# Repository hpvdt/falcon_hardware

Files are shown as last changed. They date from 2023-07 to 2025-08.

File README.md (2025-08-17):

>[!WARNING]
>This repository is no longer being maintained. All board designs for Falcon are part of their respective project repositories under HPVDT. This repository can be considered a snapshot fo the project 2023 or so.

# Falcon Hardware

These are the collected files for all the custom circuit boards for the Falcon aircraft project. All circuits were designed in KiCad 7, and the Gerber files for the circuits as ordered are included.

These systems were primarily designed by several members of HPVDT, overseen by the head of electronics. A block diagram describing their place in the overaching system has been prepared.

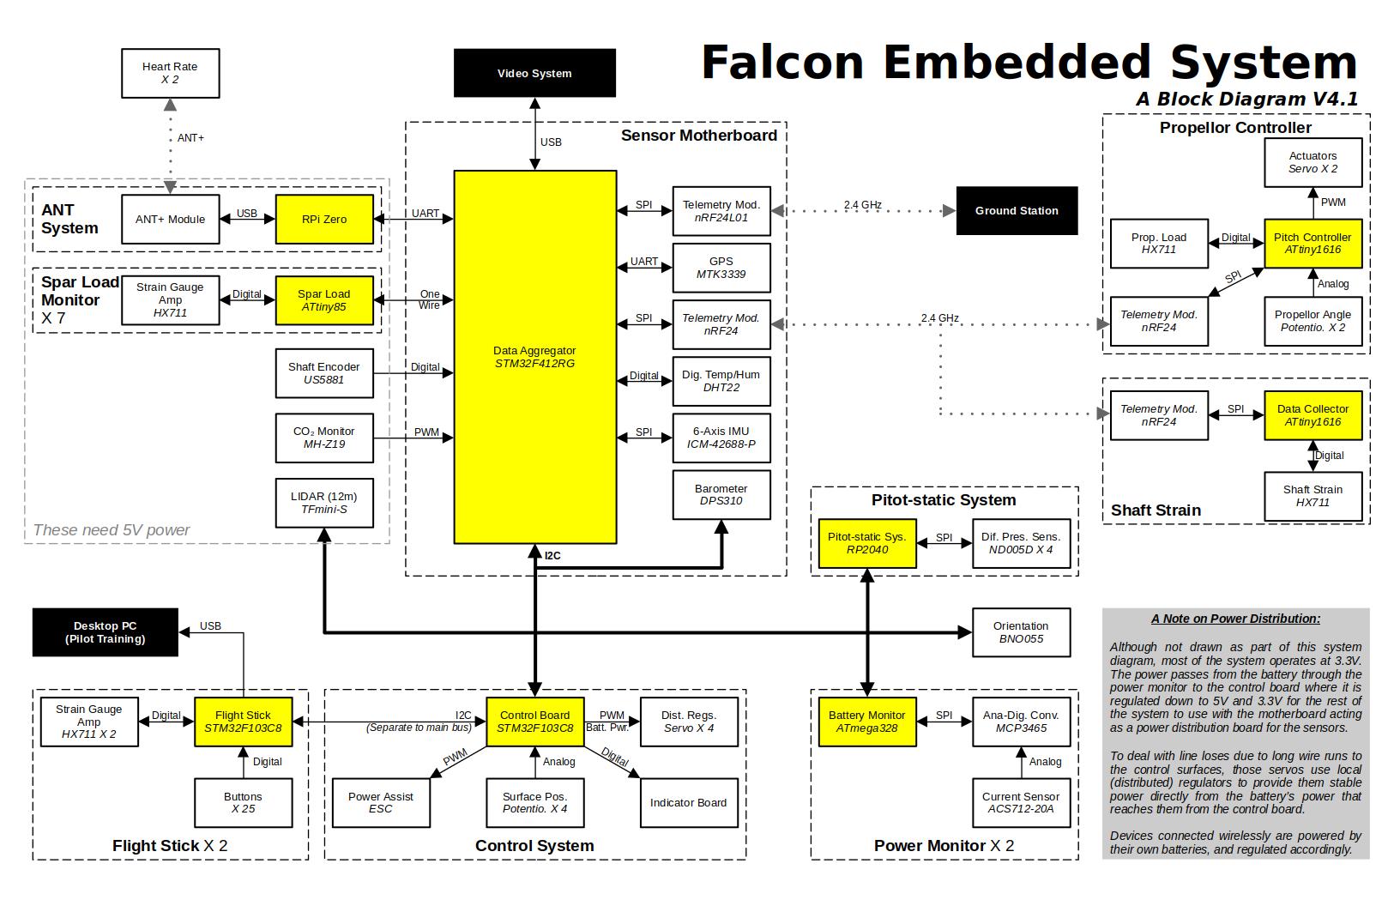
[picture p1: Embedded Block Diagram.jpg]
Embedded system block diagram


## Projects

Each folder is for a different electronics circuit/system, which are explained in the table below. 

| Folder | Project | Principal Designer |
| --- | ---| --- |
| `control` | Operates the aircraft's control surfaces | Abdullah Alsafar |
| `flight_stick` | Flight stick, pilots' primary input to the system | Aryan Ghosh |
| `indicator` | Daughter board to indicate control surface status to pilots | Abdullah Alsafar |
| `main_data` | Primary board for data collection of all sensor data | Aryan Ghosh |
| `pressure_sensor_array_atmega` | Differntial pressure array for monitoring wind (ATmega328P) | Jaden Stanshall |
| `pressure_sensor_array_rp` | Differntial pressure array for monitoring wind (RP2040) | Jaden Stanshall |
| `pressure_sensor_array_breakout` | Breakpout for our selected differential pressure sensors | Jaden Stanshall |
| `prop_pitch` | Adjusts the propellor blade pitch and monitors shaft loading | Savo Bajic |
| `servo_regulator` | Distributed servo voltage regulators | Abdullah Alsafar |
| `spar_sensor` | System to monitor the loading of our spars | Alya / Ishi |

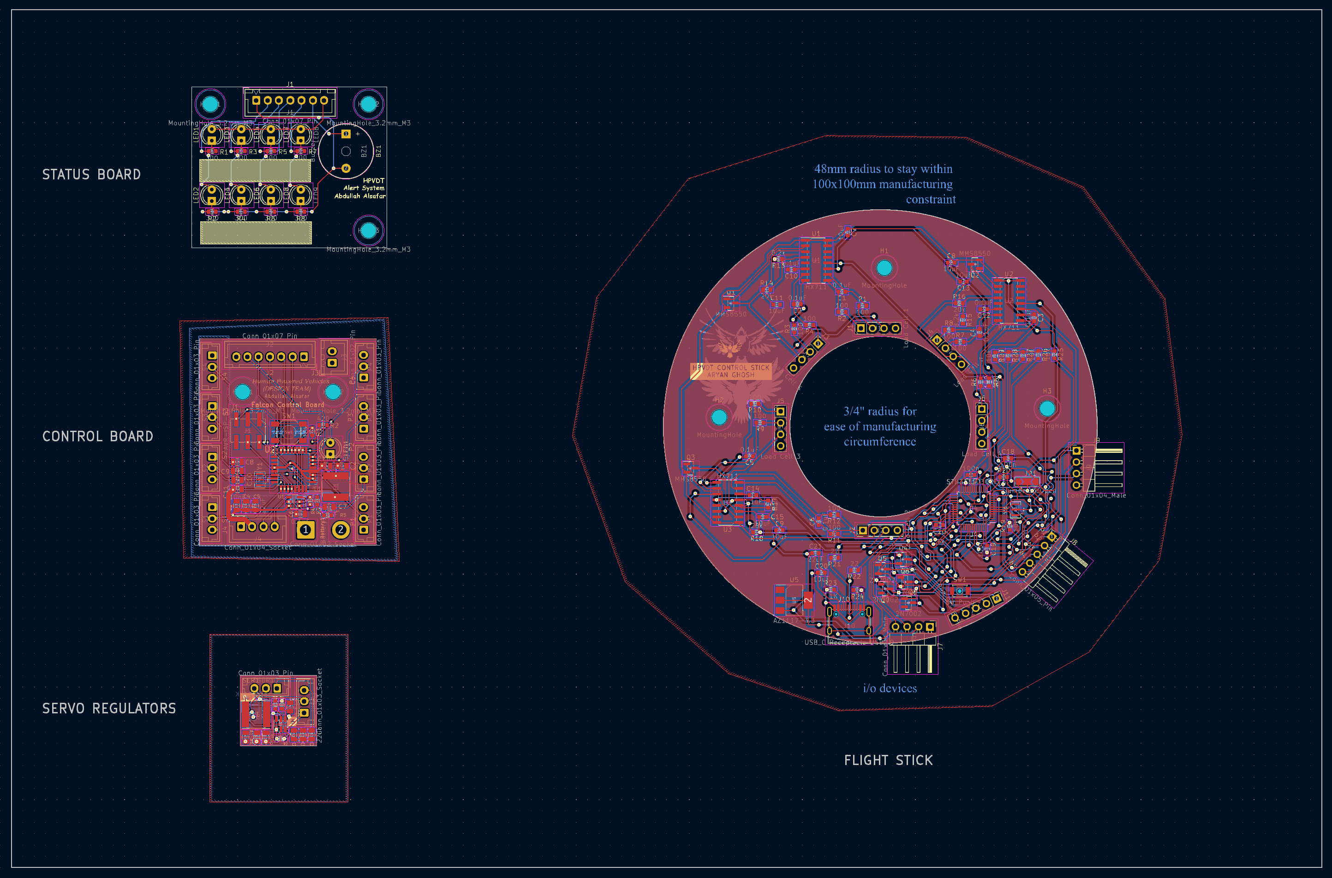
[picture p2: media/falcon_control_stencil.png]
Control system stencil / boards overview


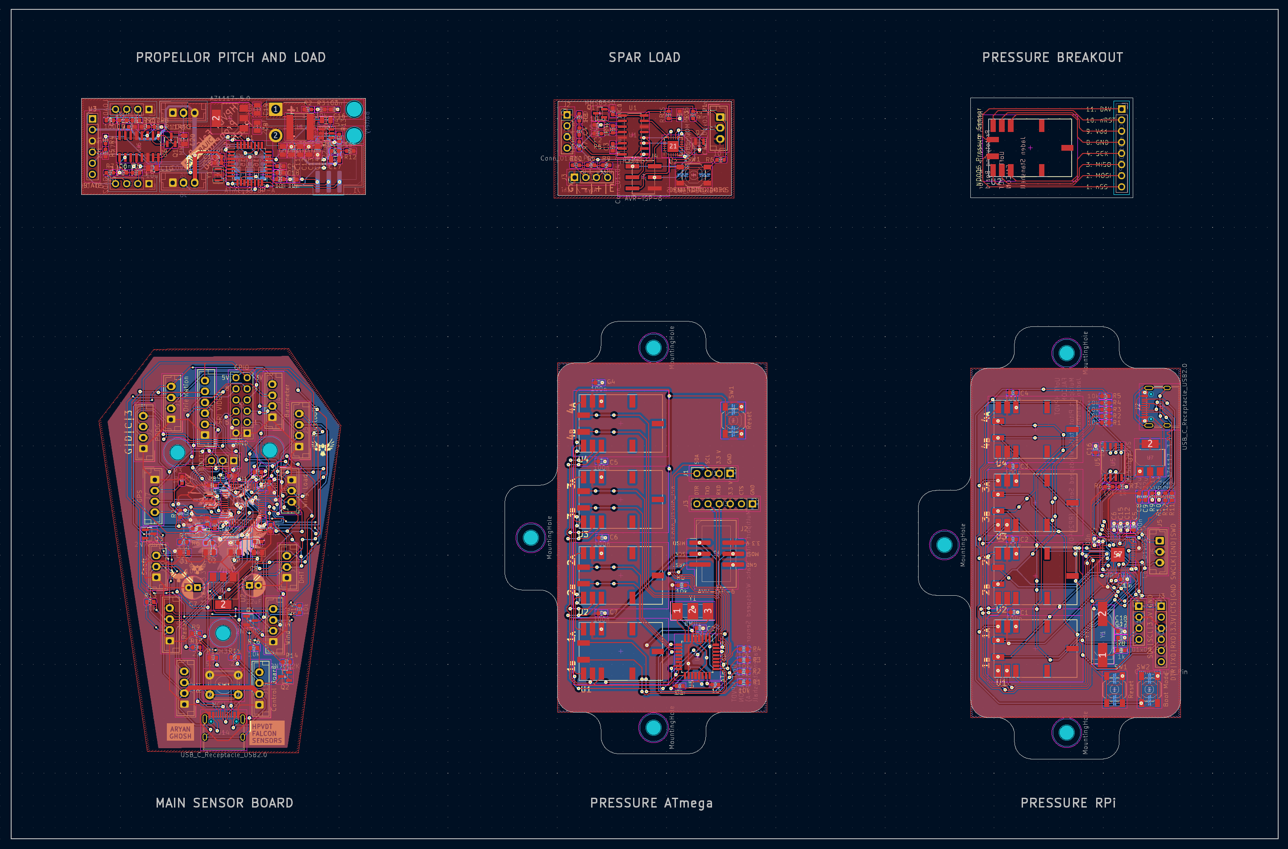
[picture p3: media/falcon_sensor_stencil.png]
Sensing system stencil / boards overview


## Additional Folders

In addition to these projects there are a couple extra folders not directly related to hardware projects present.

| Folder | Purpose | 
| --- | --- |
| `ordered_gerbers` | The manufacturing files actually used for the boards |
| `stencils` | The stencils prepared for the set of boards | 
| `media` | Media files for this repository |

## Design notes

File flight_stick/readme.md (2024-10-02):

# Falcon Aircraft Flight Stick
### In Progress

Human Powered Vehicles Design Team

November 2022

Aryan Ghosh

### Block diagram


#### Schematic Layout


### PCB 2-Layer Layout



### 3D Render of PCB Layout


## Introduction
Created for the Falcon Aircraft, the Falcon Aircraft Flight Stick (FAFS) is the first flight stick to implement **three** axes of motion detection, remain rigid, and feature up to 25 programmable buttons. This was done to accommodate the unique nature of the Human-powered falcon aircraft, where the user could control the entire aircraft with one hand, keeping the other free, while maintaining a durable and versatile design. 

The design features:
- An STM32 Microcontroller programmed with custom firmware and libraries
- An ADS131 amplifier and ADC paired with linear and torque strain gauges
- A 5x5 transistor array to feature up to 25 buttons
- Power indicators and Multi-colour LEDs to indicate device function
- USB-C connectivity to plug into a computer to use as a joystick
- STLinkV3 programmability with SWD and UART

ReadMe in progress...

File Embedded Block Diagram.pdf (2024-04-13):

## Shaft Strain

Pitot-static Sys.
RP2040

Dif. Pres. Sens.
ND005D X 4

LIDAR (12m)
TFmini-S

Flight Stick
STM32F103C8

Strain Gauge
Amp
HX711 X 2

Data Aggregator
STM32F412RG

Orientation
BNO055

Barometer
DPS310

GPS
MTK3339
ANT+ Module | RPi Zero

Strain Gauge
Amp
HX711

Spar Load
ATtiny85

Dist. Regs.
Servo X 4

Control Board
STM32F103C8

Surface Pos.
Potentio. X 4 | Indicator Board

Prop. Load
HX711

Buttons
X 25

Actuators
Servo X 2

Pitch Controller
ATtiny1616

Telemetry Mod.
nRF24

Telemetry Mod.
nRF24L01

Shaft Encoder
US5881

Video System Heart Rate
X 2

Battery Monitor
ATmega328

Ana-Dig. Conv.
MCP3465

Current Sensor
ACS712-20A

Dig. Temp/Hum
DHT22

Ground Station

## Spar Load Monitor

X 7

## ANT System

## Flight Stick X 2

## Pitot-static System

## Propellor Controller

Control System | Power Monitor X 2

SPI

SPI

One
Wire

UART

UART

Digital

USB

Digital

Digital

Digital

Digital

2.4 GHz

I2C

Digital | Analog | Analog

PWM

Shaft Strain
HX711

Data Collector
ATtiny1616

Telemetry Mod.
nRF24

SPI

Digital

SPI

Digital

PWM
Batt. Pwr.

## Sensor Motherboard

2.4 GHz

I2C
(Separate to main bus)

A Note on Power Distribution:

Although not drawn as part of this system diagram, most of the system operates at 3.3V. The power passes from the battery through the power monitor to the control board where it is regulated down to 5V and 3.3V for the rest of the system to use with the motherboard acting as a power distribution board for the sensors.

To deal with line loses due to long wire runs to the control surfaces, those servos use local (distributed) regulators to provide them stable power directly from the battery’s power that reaches them from the control board.

Devices connected wirelessly are powered by their own batteries, and regulated accordingly.

## These need 5V power

# Falcon Embedded System

## A Block Diagram V4.1

Telemetry Mod.
nRF24

SPI

6-Axis IMU
ICM-42688-P

SPI

SPI

Power Assist
ESC

PWM

CO2 Monitor
MH-Z19

PWM

ANT+

Desktop PC
(Pilot Training)

Propellor Angle
Potentio. X 2

Analog

USB

USB

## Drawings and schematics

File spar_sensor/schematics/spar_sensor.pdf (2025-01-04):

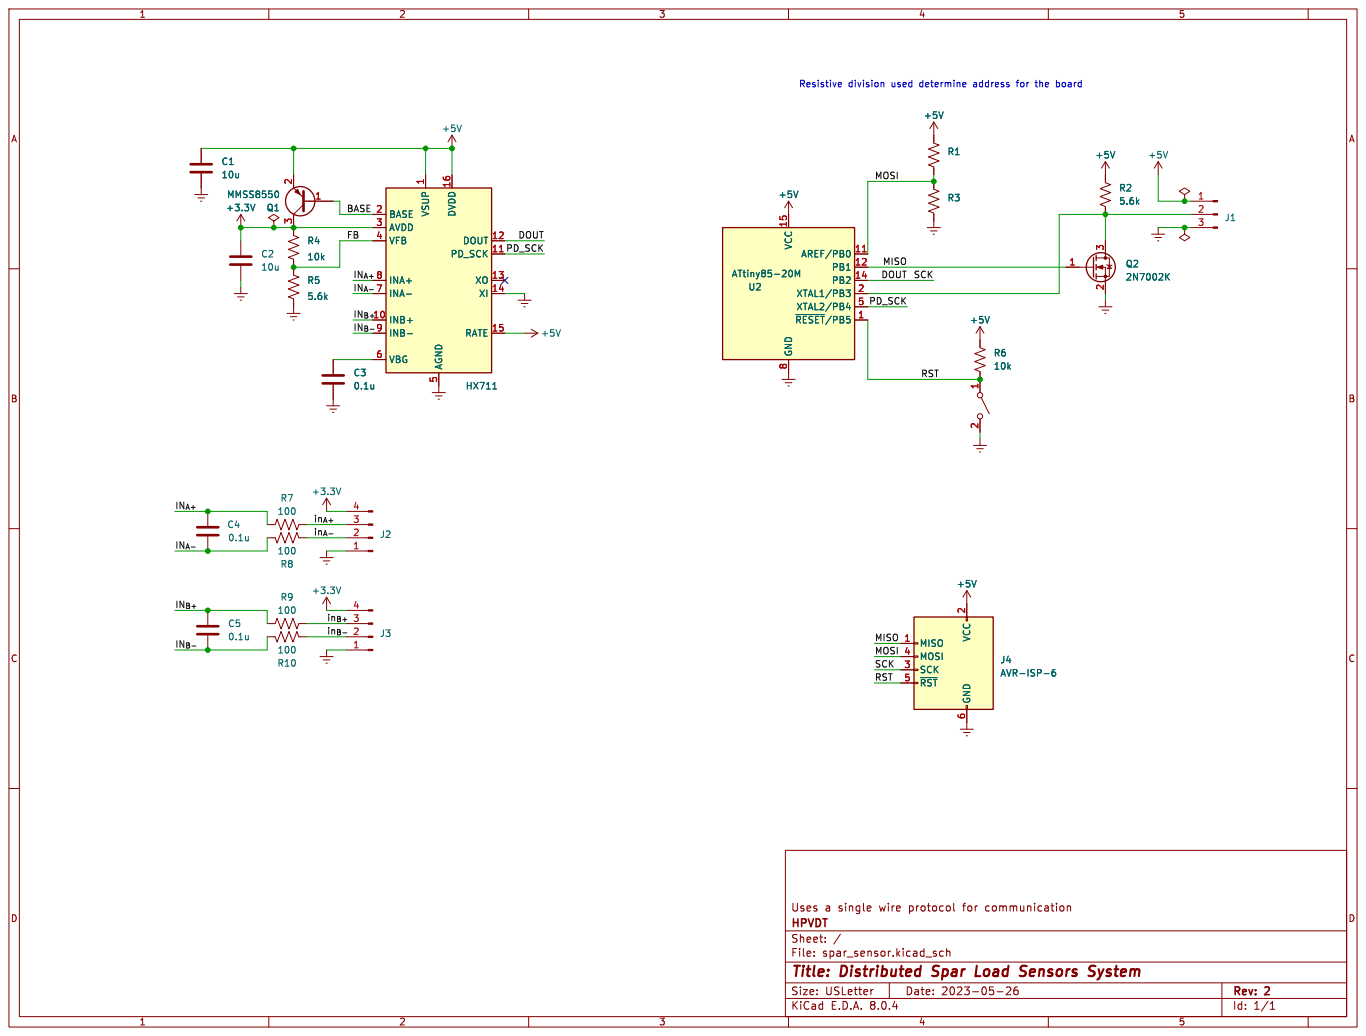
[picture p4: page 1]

2 SCK 3 MOSI 4 ~{RST} 5 GND

Id: 1/1 Title: Distributed Spar Load Sensors System

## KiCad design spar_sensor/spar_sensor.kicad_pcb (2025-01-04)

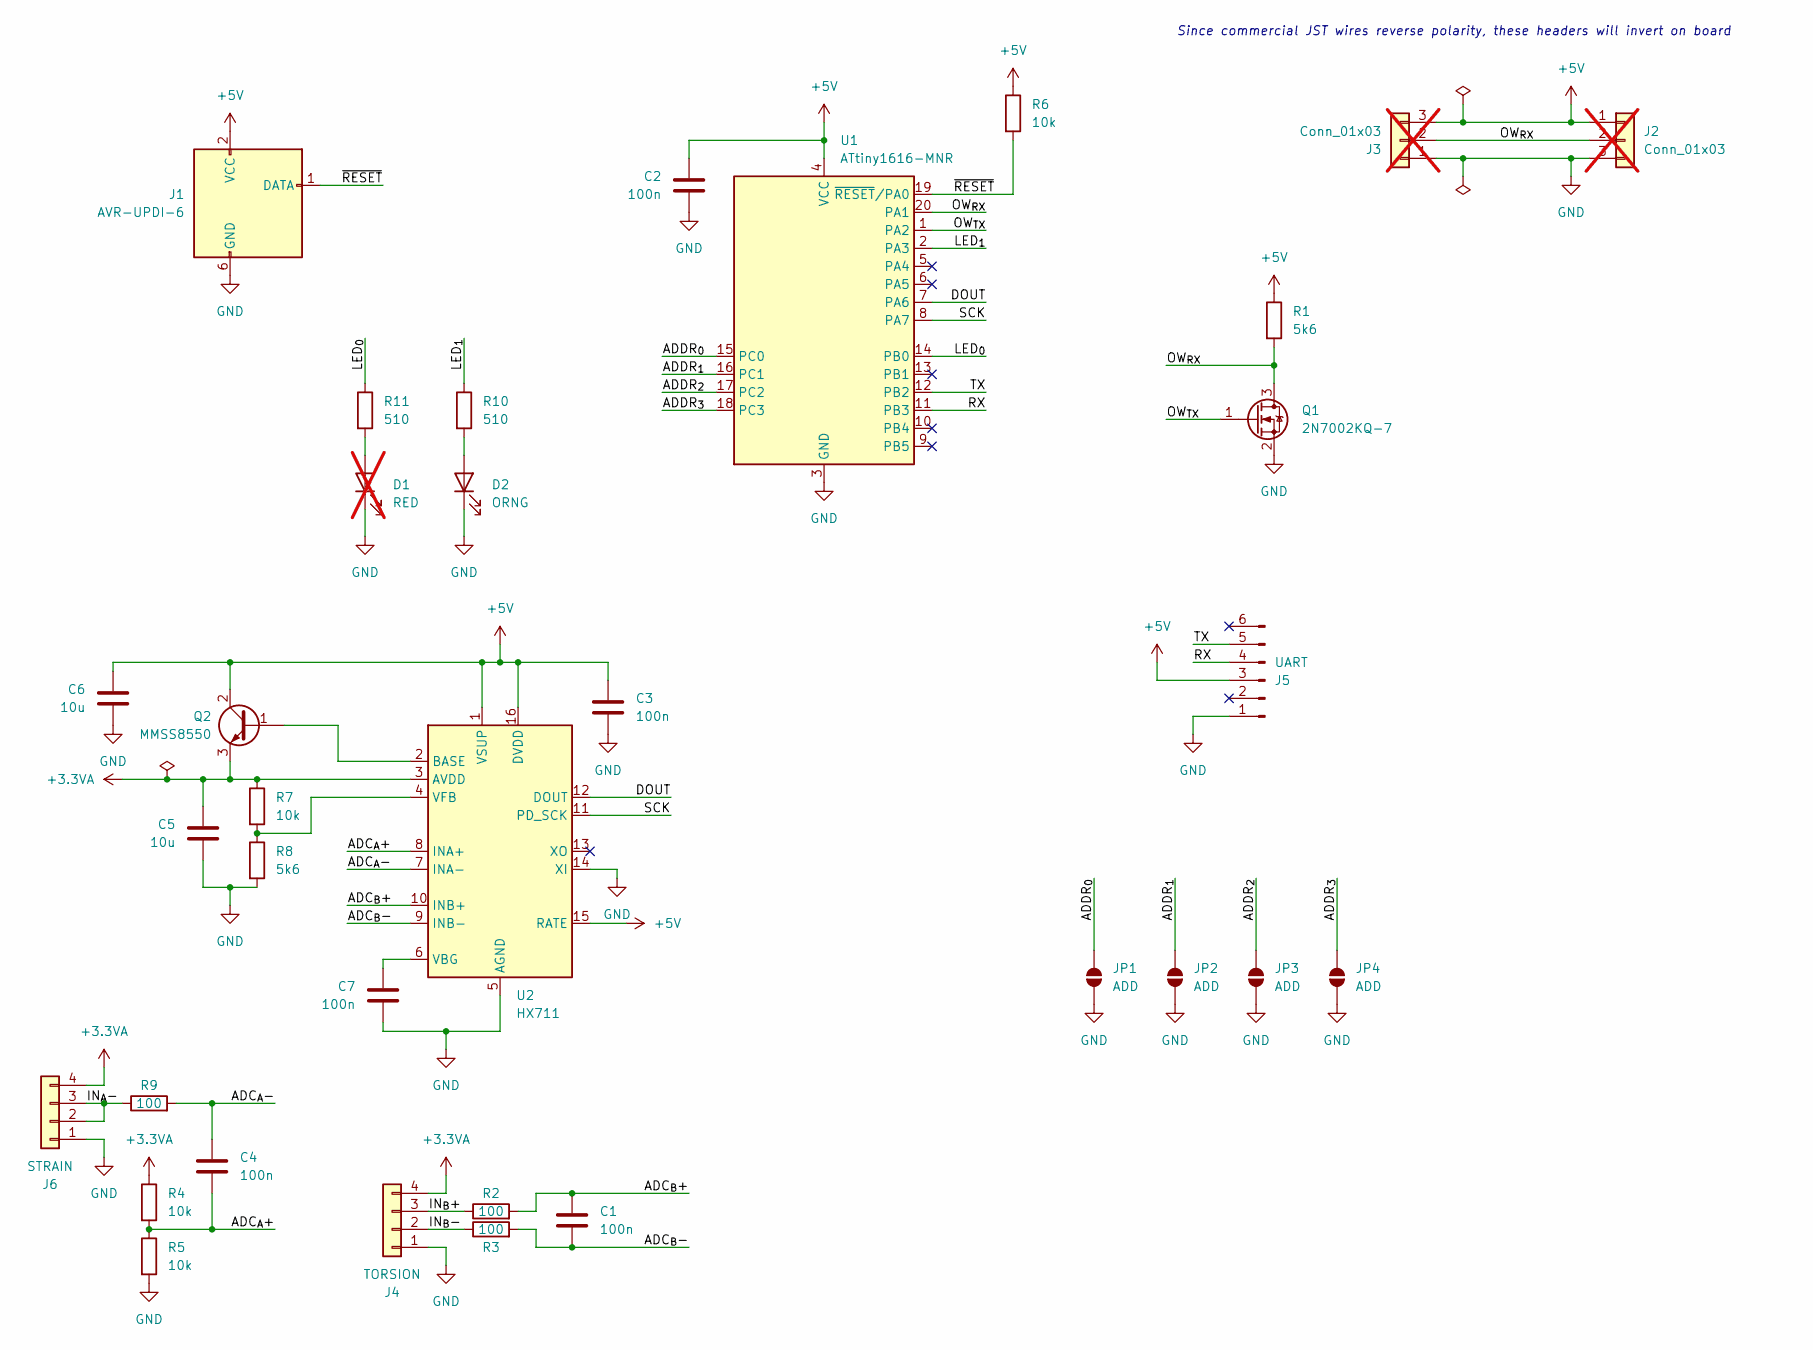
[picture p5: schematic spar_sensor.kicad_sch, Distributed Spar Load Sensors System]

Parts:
C1, C2, C3, C4, C7: 100n; C_0402_1005Metric; LCSC C5448875
C5, C6: 10u; C_0603_1608Metric; LCSC C5360828
D1: RED; LED_0805_2012Metric; LCSC N/A; not fitted
D2: ORNG; LED_0805_2012Metric; LCSC C2292
J1: AVR-UPDI-6; Tag-Connect_TC2030-IDC-NL_2x03_P1.27mm_Vertical; LCSC N/A
J2, J3: Conn_01x03; JST_EH_B3B-EH-A_1x03_P2.50mm_Vertical; LCSC C398546; not fitted
J4: TORSION; PinHeader_1x04_P2.00mm_Vertical; LCSC N/A
J5: UART; PinHeader_1x06_P2.54mm_Vertical; LCSC N/A
J6: STRAIN; PinHeader_1x04_P2.00mm_Vertical; LCSC N/A
JP1, JP2, JP3, JP4: ADD; SolderJumper-2_P1.3mm_Open_TrianglePad1.0x1.5mm; LCSC N/A
Q1: 2N7002KQ-7; SOT-23; LCSC C111971
Q2: MMSS8550; SOT-23; LCSC C192429
R1, R8: 5k6; R_0402_1005Metric; LCSC C340537
R2, R3, R9: 100; R_0402_1005Metric; LCSC C606168
R4, R5: 10k; R_0402_1005Metric; LCSC C191915
R6, R7: 10k; R_0402_1005Metric; LCSC C723353
R10, R11: 510; R_0402_1005Metric; LCSC C2991609
U1: ATtiny1616-MNR; VQFN-20-1EP_3x3mm_P0.4mm_EP1.7x1.7mm; LCSC C507118
U2: HX711; SOP-16_3.9x9.9mm_P1.27mm; LCSC C6705483

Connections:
+3.3VA: C5.1, J4.4, J6.4, Q2.3 (E), R4.1, R7.1, U2.3 (AVDD)
+5V: C2.1, C3.1, C6.1, J1.2 (VCC), J2.1, J3.3, J5.3, Q2.2 (C), R1.1, R6.1, U1.4 (VCC), U2.1 (VSUP), U2.15 (RATE), U2.16 (DVDD)
/ADC_{A}+: C4.2, R4.2, R5.1, U2.8 (INA+)
/ADC_{A}-: C4.1, R9.2, U2.7 (INA-)
/ADC_{B}+: C1.1, R2.2, U2.10 (INB+)
/ADC_{B}-: C1.2, R3.2, U2.9 (INB-)
/ADDR_{0}: JP1.2 (B), U1.15 (PC0)
/ADDR_{1}: JP2.2 (B), U1.16 (PC1)
/ADDR_{2}: JP3.2 (B), U1.17 (PC2)
/ADDR_{3}: JP4.2 (B), U1.18 (PC3)
/DOUT: U1.7 (PA6), U2.12 (DOUT)
/IN_{A}-: J6.2, J6.3, R9.1
/IN_{B}+: J4.3, R2.1
/IN_{B}-: J4.2, R3.1
/LED_{0}: R11.1, U1.14 (PB0)
/LED_{1}: R10.1, U1.2 (PA3)
/OW_{RX}: J2.2, J3.2, Q1.3 (D), R1.2, U1.20 (PA1)
/OW_{TX}: Q1.1 (G), U1.1 (PA2)
/RX: J5.4, U1.11 (PB3)
/SCK: U1.8 (PA7), U2.11 (PD_SCK)
/TX: J5.5, U1.12 (PB2)
/~RESET: J1.1 (DATA), R6.2, U1.19 (~RESET/PA0)
GND: C2.2, C3.2, C5.2, C6.2, C7.2, D1.1 (K), D2.1 (K), J1.6 (GND), J2.3, J3.1, J4.1, J5.1, J6.1, JP1.1 (A), JP2.1 (A), JP3.1 (A), JP4.1 (A), Q1.2 (S), R5.2, R8.2, U1.3 (GND), U1.21 (GND), U2.5 (AGND), U2.14 (XI)
unnamed: D1.2 (A), R11.2
unnamed: D2.2 (A), R10.2
unnamed: Q2.1 (B), U2.2 (BASE)
unnamed: C7.1, U2.6 (VBG)
unnamed: R7.2, R8.1, U2.4 (VFB)

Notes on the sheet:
Since commercial JST wires reverse polarity, these headers will invert on board

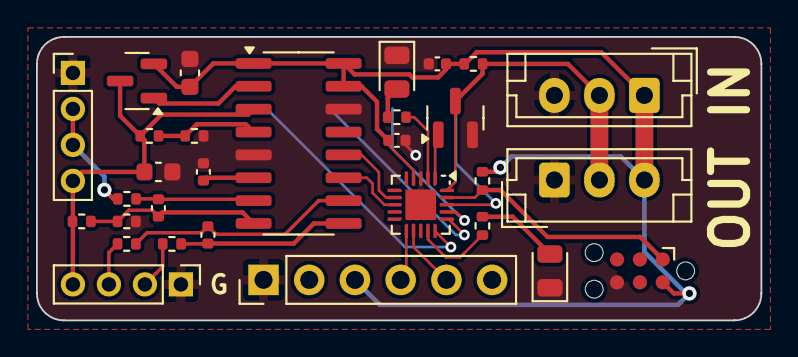
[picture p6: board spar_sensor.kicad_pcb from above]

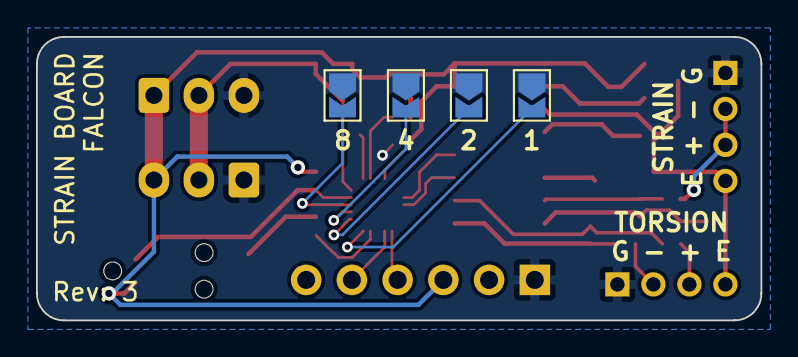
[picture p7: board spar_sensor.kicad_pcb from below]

Board: 2 copper layers, 40.2 x 15.8 mm, 34 parts (4 on the bottom side), 28 nets.

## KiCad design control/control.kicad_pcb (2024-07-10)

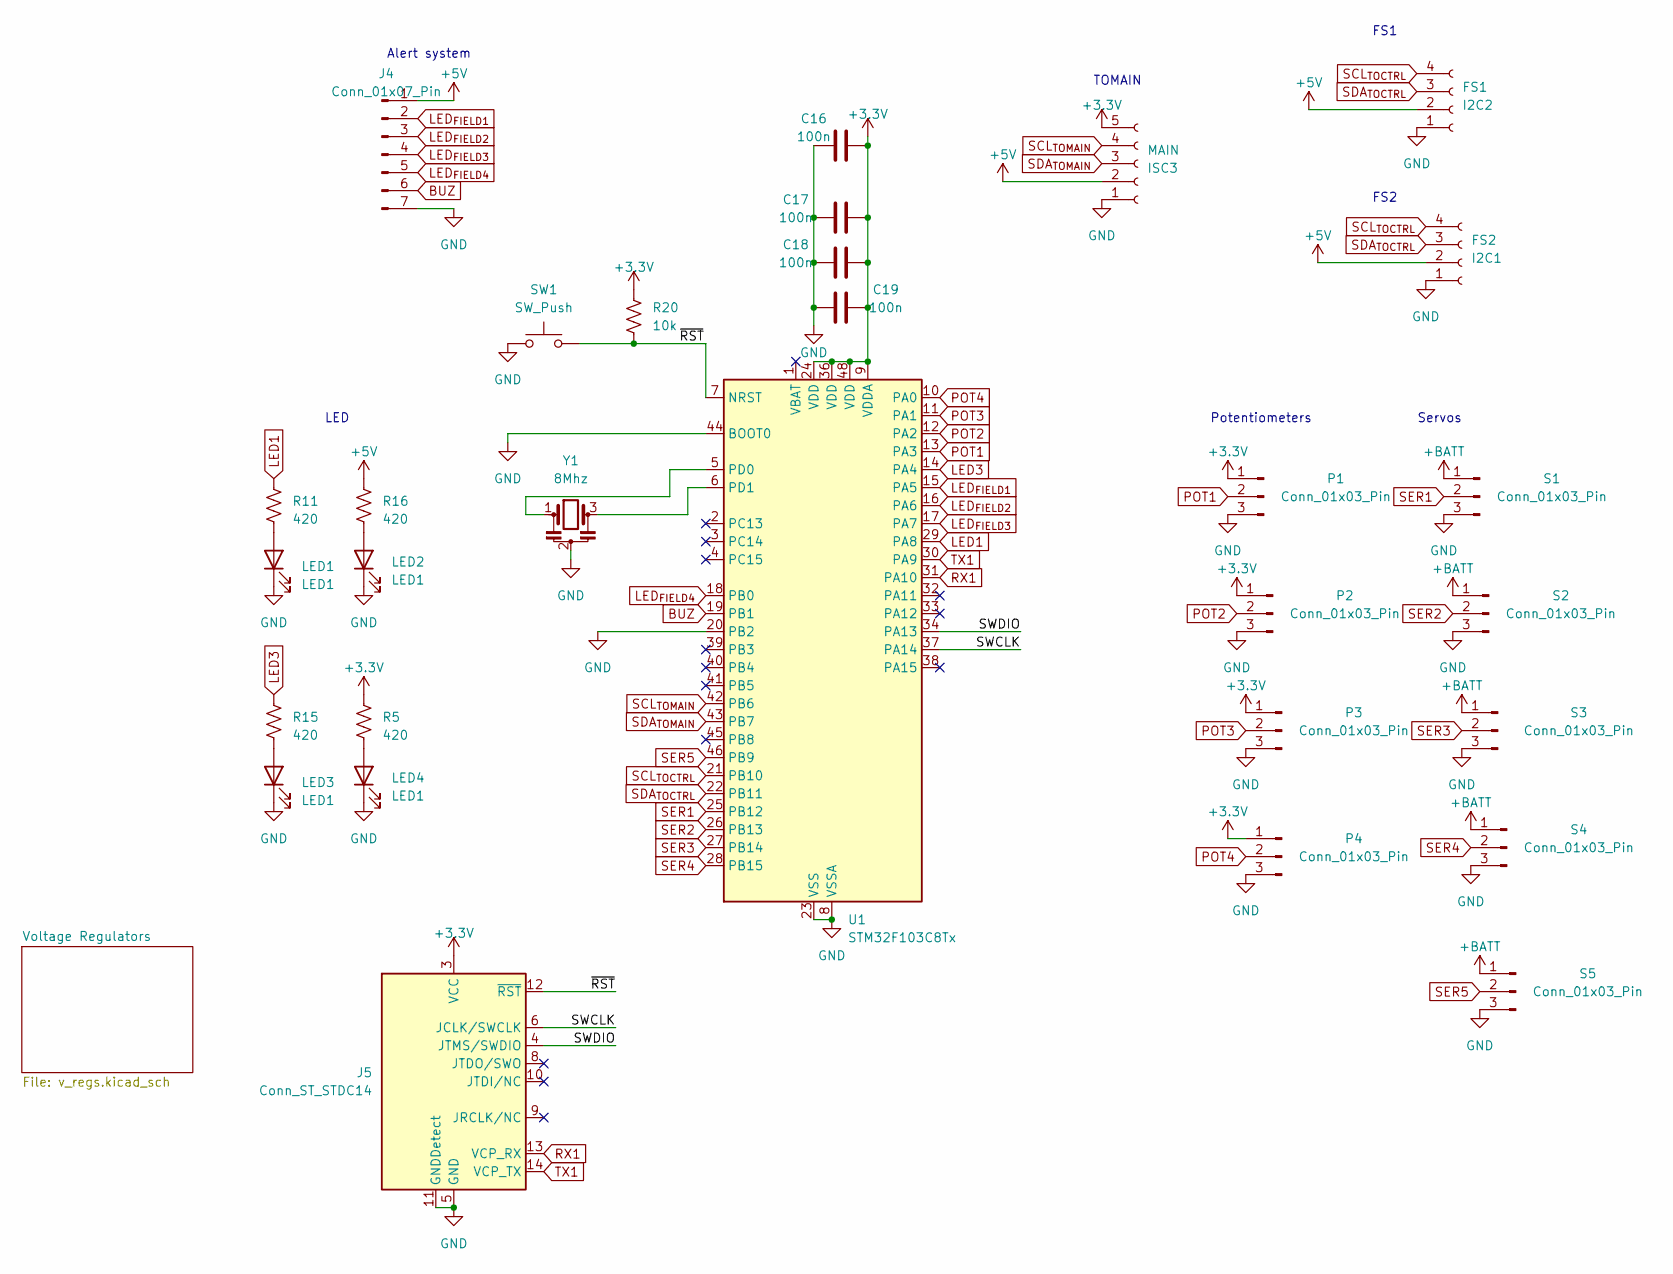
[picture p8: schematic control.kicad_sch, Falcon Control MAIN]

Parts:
C16, C17, C18, C19: 100n; C_0603_1608Metric
I2C1: FS2; JST_XH_B4B-XH-A_1x04_P2.50mm_Vertical
I2C2: FS1; JST_XH_B4B-XH-A_1x04_P2.50mm_Vertical
ISC3: MAIN; JST_XH_B5B-XH-A_1x05_P2.50mm_Vertical
J4: Conn_01x07_Pin; JST_XH_B7B-XH-A_1x07_P2.50mm_Vertical
J5: Conn_ST_STDC14; PinHeader_2x07_P1.27mm_Vertical_SMD
LED1, LED2, LED3, LED4: LED1; LED_0805_2012Metric_Pad1.15x1.40mm_HandSolder
P1, P2, P3, P4: Conn_01x03_Pin; JST_EH_B3B-EH-A_1x03_P2.50mm_Vertical
R5, R11, R15, R16: 420; R_0603_1608Metric
R20: 10k; R_0603_1608Metric
S1, S2, S3, S4, S5: Conn_01x03_Pin; JST_EH_B3B-EH-A_1x03_P2.50mm_Vertical
SW1: SW_Push; SW_SPST_B3U-1000P-B
U1: STM32F103C8Tx; LQFP-48_7x7mm_P0.5mm
Y1: 8Mhz; Resonator_SMD_Murata_CSTxExxV-3Pin_3.0x1.1mm

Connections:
+5V: I2C1.2, I2C2.2, ISC3.2, J4.1, R16.2; also elsewhere on the board
/SWCLK: J5.6 (JCLK/SWCLK), U1.37 (PA14)
/SWDIO: J5.4 (JTMS/SWDIO), U1.34 (PA13)
/~RST: J5.12 (~RST), U1.7 (NRST); also elsewhere on the board
BUZ: J4.6, U1.19 (PB1)
LED1: R11.2, U1.29 (PA8)
LED3: R15.2, U1.14 (PA4)
LED_{FIELD1}: J4.2, U1.15 (PA5)
LED_{FIELD2}: J4.3, U1.16 (PA6)
LED_{FIELD3}: J4.4, U1.17 (PA7)
LED_{FIELD4}: J4.5, U1.18 (PB0)
unnamed: LED1.2 (A), R11.1
unnamed: LED2.2 (A), R16.1
unnamed: LED3.2 (A), R15.1
unnamed: LED4.2 (A), R5.1
unnamed: U1.5 (PD0), Y1.1
unnamed: U1.6 (PD1), Y1.3
POT1: P1.2, U1.13 (PA3)
POT2: P2.2, U1.12 (PA2)
POT3: P3.2, U1.11 (PA1)
POT4: P4.2, U1.10 (PA0)
RX1: J5.13 (VCP_RX), U1.31 (PA10)
SCL_{TOCTRL}: I2C1.4, I2C2.4, U1.21 (PB10)
SCL_{TOMAIN}: ISC3.4, U1.42 (PB6)
SDA_{TOCTRL}: I2C1.3, I2C2.3, U1.22 (PB11)
SDA_{TOMAIN}: ISC3.3, U1.43 (PB7)
SER1: S1.2, U1.25 (PB12)
SER2: S2.2, U1.26 (PB13)
SER3: S3.2, U1.27 (PB14)
SER4: S4.2, U1.28 (PB15)
SER5: S5.2, U1.46 (PB9)
TX1: J5.14 (VCP_TX), U1.30 (PA9)

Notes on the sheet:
FS1
Servos
Alert system
FS2
TOMAIN
Potentiometers
LED

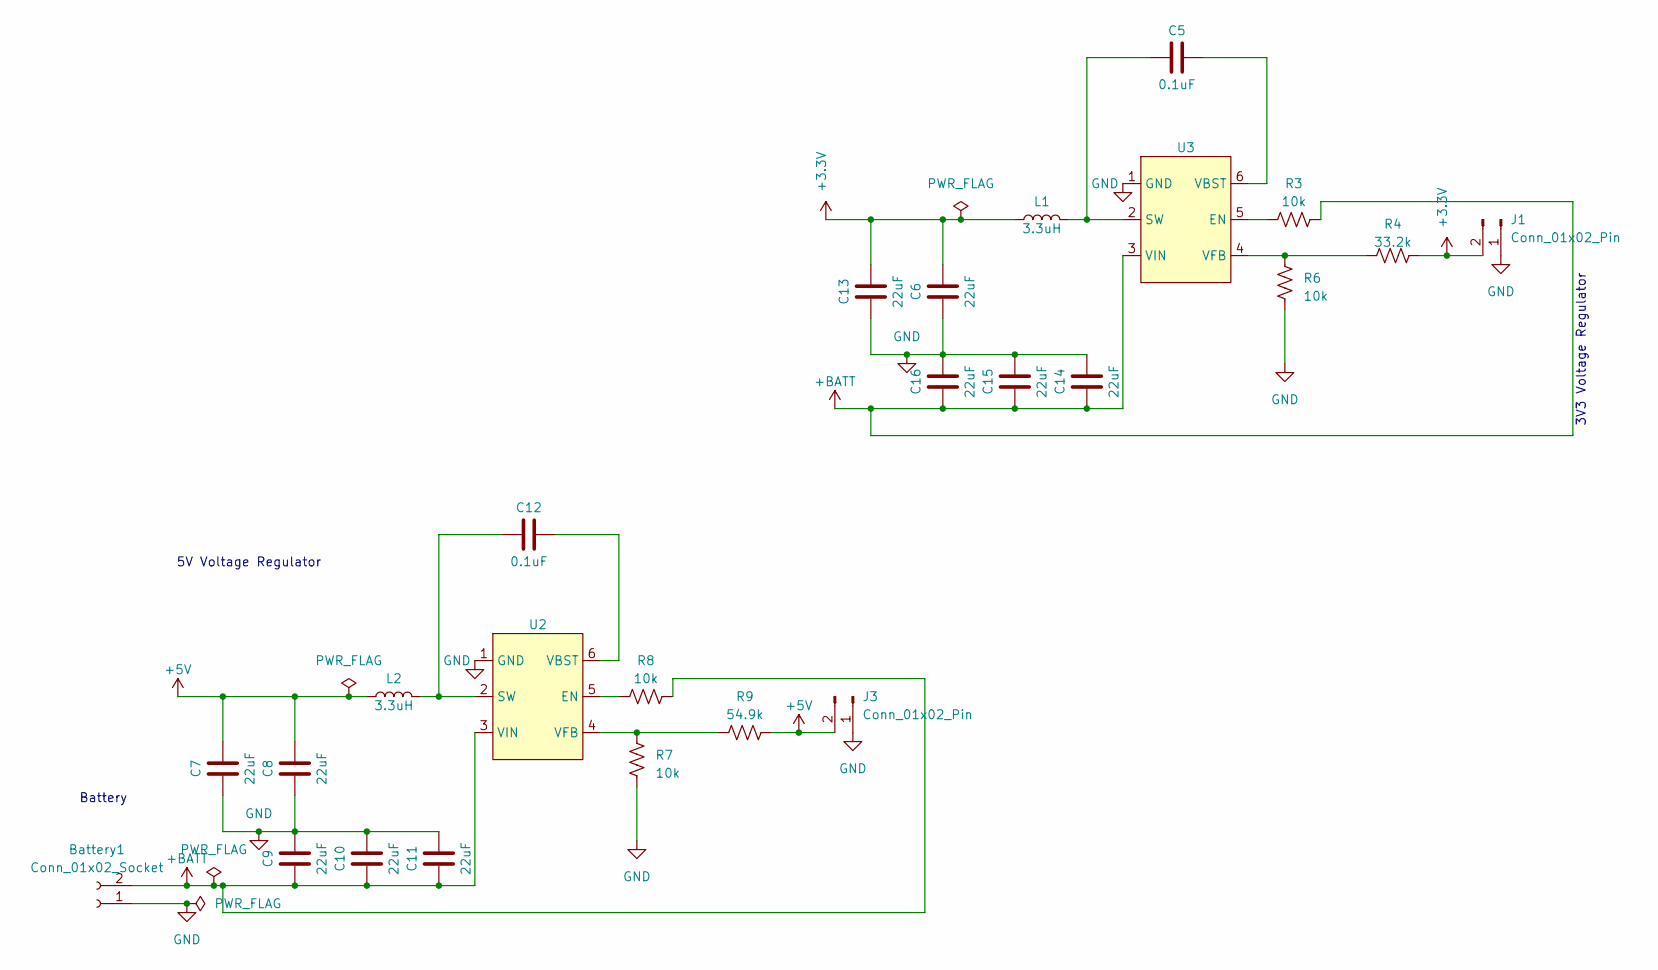
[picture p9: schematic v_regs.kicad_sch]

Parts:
Battery1: Conn_01x02_Socket; AMASS_XT60-M_1x02_P7.20mm_Vertical
C5, C12: 0.1uF; C_0805_2012Metric
C6, C7, C8, C9, C10, C11, C13, C14, C15, C16: 22uF; C_0805_2012Metric
J1, J3: Conn_01x02_Pin; JST_XH_B2B-XH-A_1x02_P2.50mm_Vertical
L1, L2: 3.3uH; L_Taiyo-Yuden_NR-60xx
R3, R6, R7, R8: 10k; R_0603_1608Metric
R4: 33.2k; R_0603_1608Metric
R9: 54.9k; R_0603_1608Metric
U2, U3: TSOT-23-6

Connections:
+5V: C7.2, C8.2, J3.2, L2.1, R9.1; also elsewhere on the board
unnamed: R8.1, U2.5 (EN)
unnamed: C12.1, L2.2, U2.2 (SW)
unnamed: C12.2, U2.6 (VBST)
unnamed: R7.2, R9.2, U2.4 (VFB)
unnamed: R3.1, U3.5 (EN)
unnamed: C5.1, L1.2, U3.2 (SW)
unnamed: C5.2, U3.6 (VBST)
unnamed: R4.2, R6.2, U3.4 (VFB)

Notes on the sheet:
5V Voltage Regulator
3V3 Voltage Regulator
Battery

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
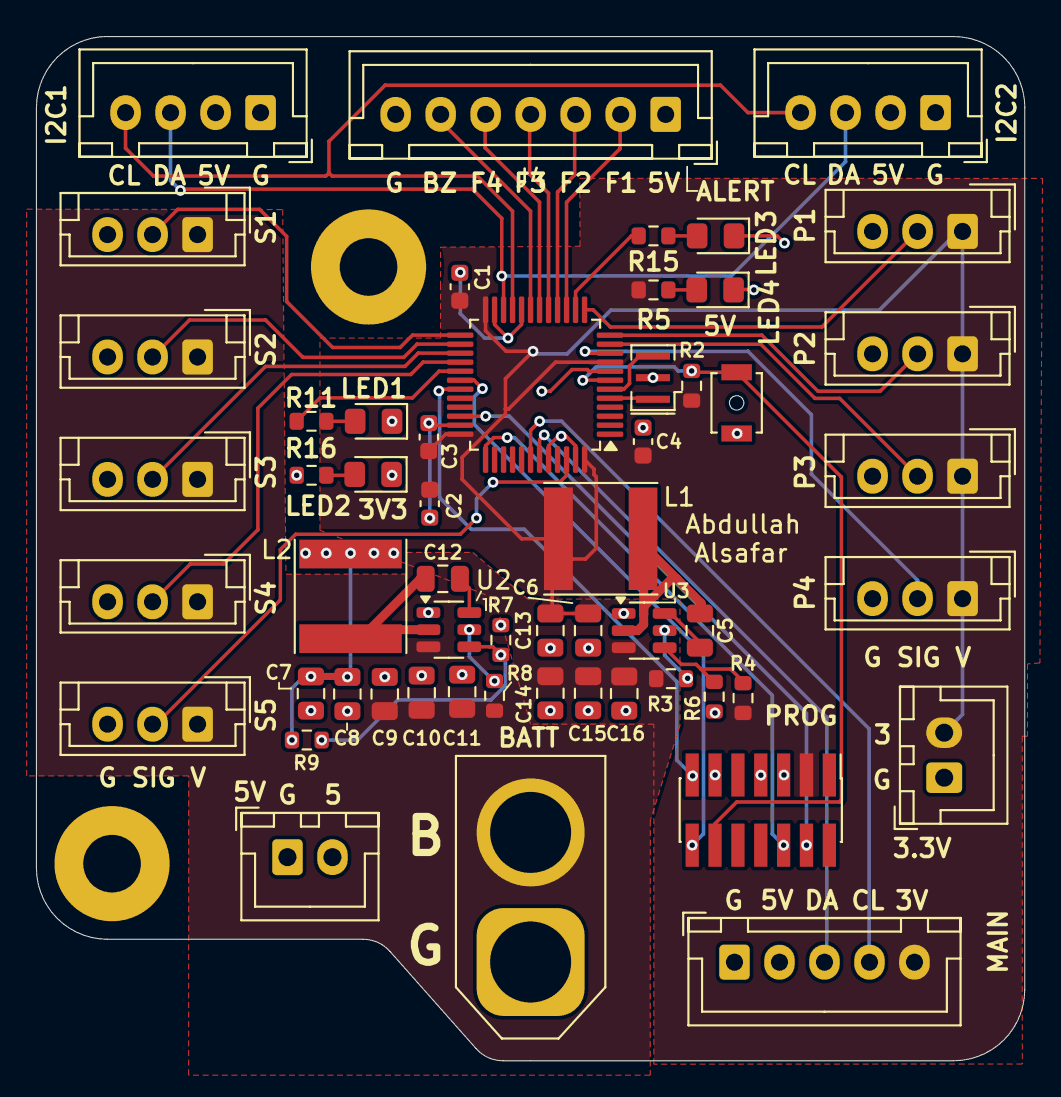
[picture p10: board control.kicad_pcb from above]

Board: 2 copper layers, 54.9 x 56.9 mm, 55 parts (0 on the bottom side), 43 nets.

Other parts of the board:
C1, C2, C3, C4: 100n; C_0603_1608Metric
R2: 10k; R_0603_1608Metric
SW2: SW_Push; SW_SPST_B3U-1000P-B

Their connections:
/~RST: R2.2, SW2.2; also elsewhere on the board

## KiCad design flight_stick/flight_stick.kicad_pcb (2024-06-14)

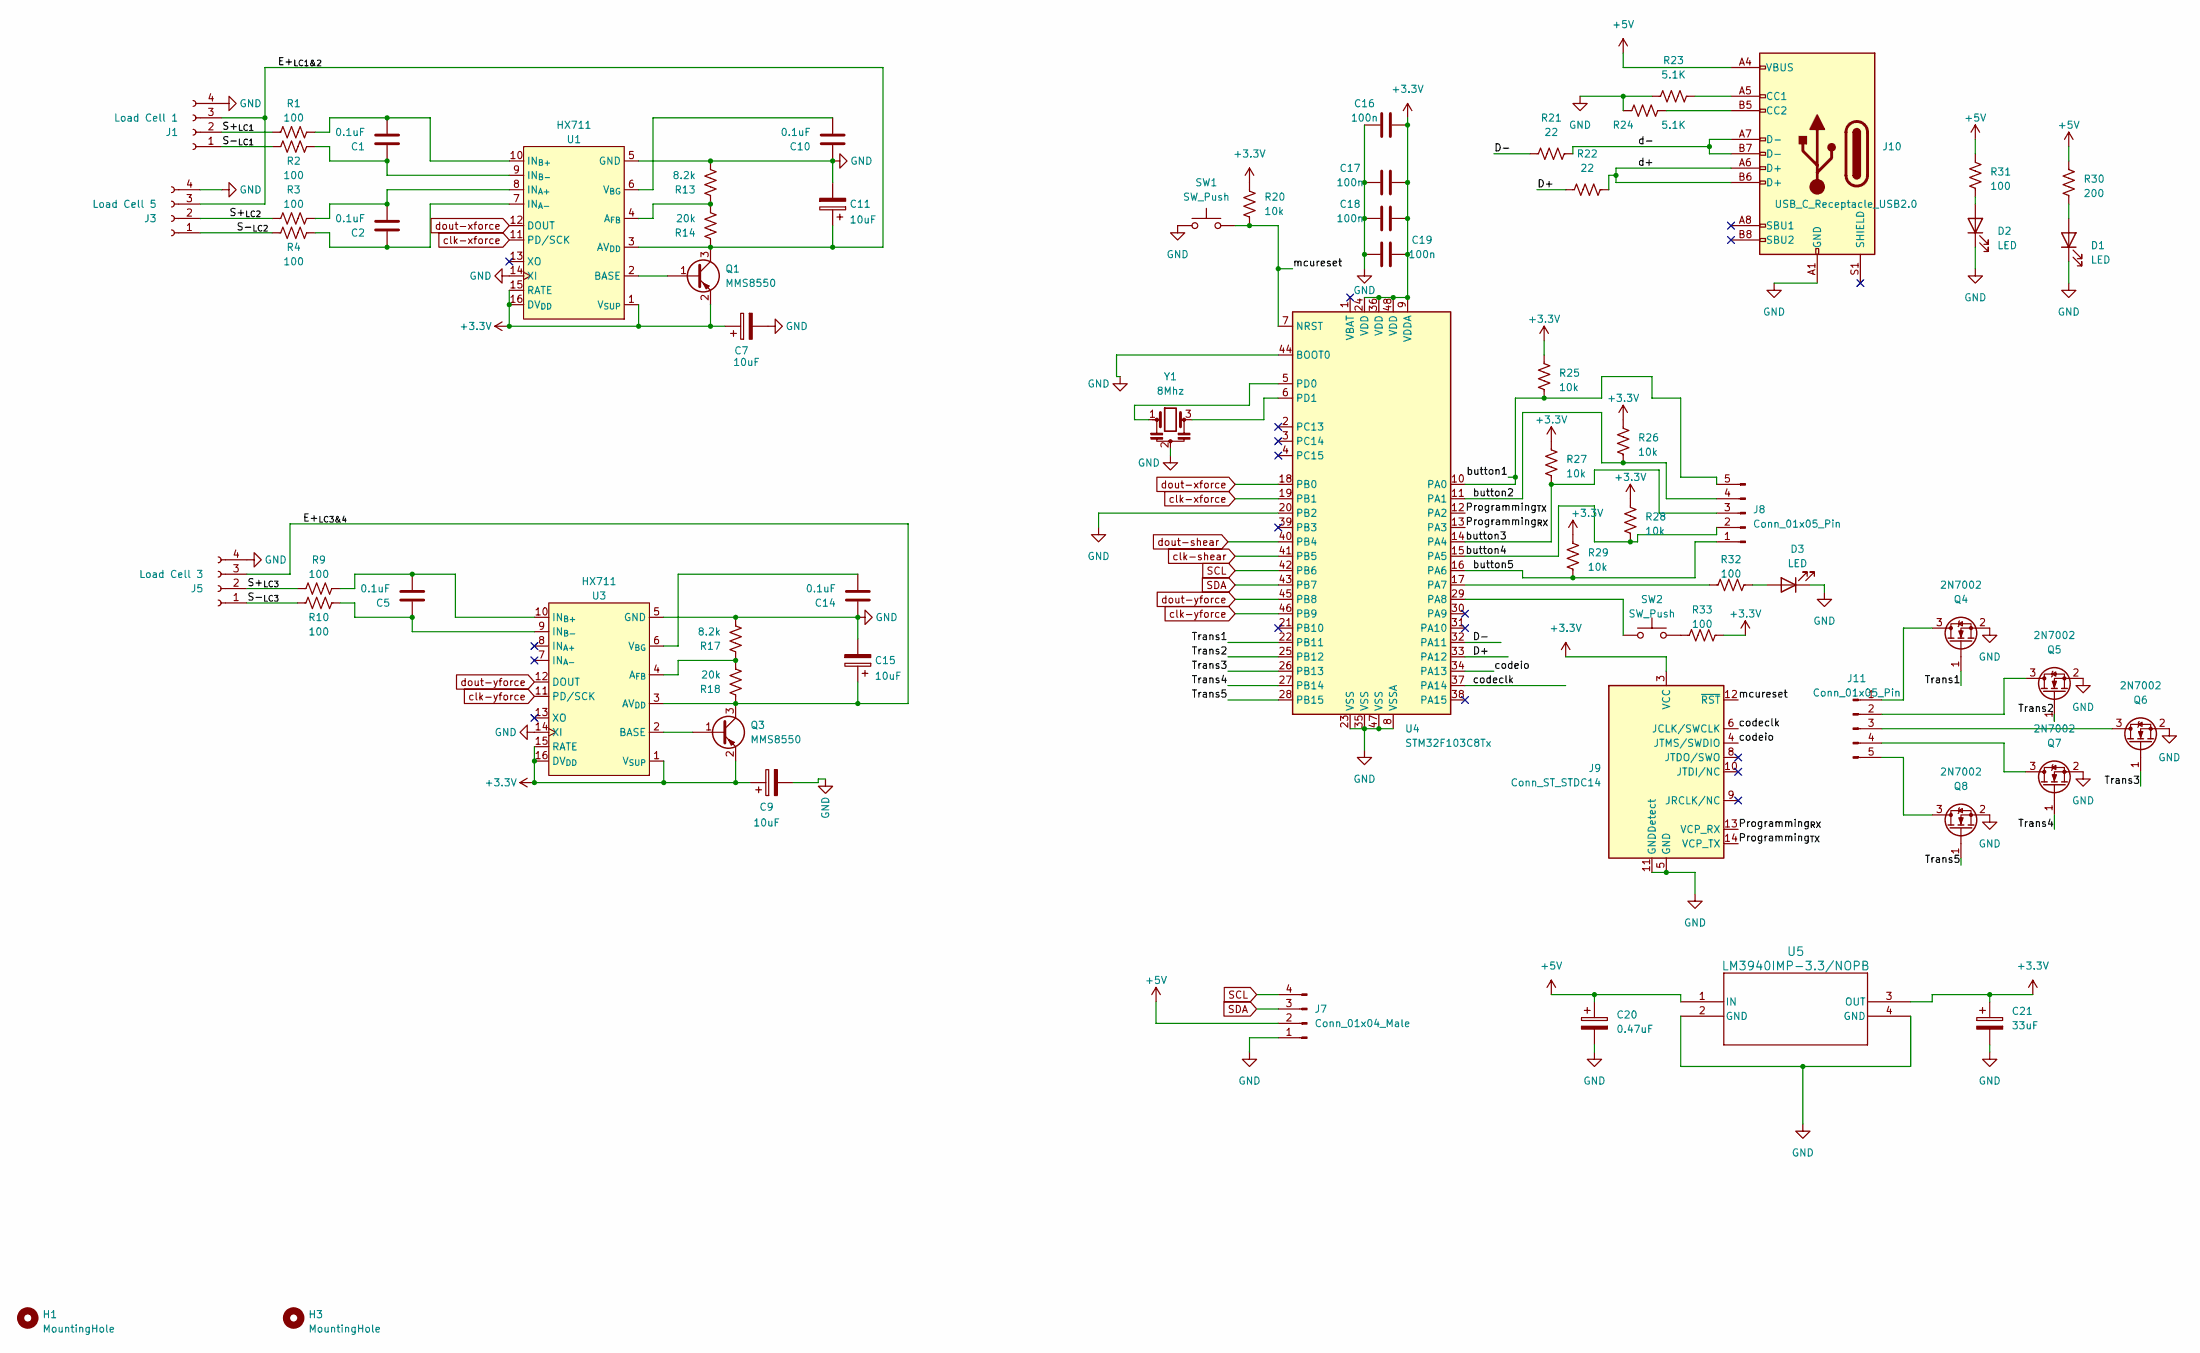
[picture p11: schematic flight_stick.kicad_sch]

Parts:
C1, C2, C5, C10, C14: 0.1uF; C_0603_1608Metric
C7, C9, C11, C15: 10uF; C_0603_1608Metric
C16, C17, C18, C19: 100n; C_0603_1608Metric
C20: 0.47uF; C_0603_1608Metric
C21: 33uF; C_0603_1608Metric
D1, D2, D3: LED; LED_2010_5025Metric
H1, H3: MountingHole; MountingHole_3.2mm_M3_ISO7380
J1: Load Cell 1; PinHeader_1x04_P1.00mm_Vertical
J3: Load Cell 5; PinHeader_1x04_P1.00mm_Vertical
J5: Load Cell 3; PinHeader_1x04_P1.00mm_Vertical
J7: Conn_01x04_Male; JST_XH_B4B-XH-A_1x04_P2.50mm_Vertical
J8: Conn_01x05_Pin; PinHeader_1x05_P2.54mm_Horizontal
J9: Conn_ST_STDC14; PinHeader_2x07_P1.27mm_Vertical_SMD
J10: USB_C_Receptacle_USB2.0; USB_C_Receptacle_HRO_TYPE-C-31-M-12
J11: Conn_01x05_Pin; PinHeader_1x05_P2.54mm_Vertical
Q1, Q3: MMS8550; SOT-23
Q4, Q5, Q6, Q7, Q8: 2N7002; SOT-23
R1, R2, R3, R4, R9, R10, R31, R32, R33: 100; R_0603_1608Metric
R13, R17: 8.2k; R_0603_1608Metric
R14, R18: 20k; R_0603_1608Metric
R20, R25, R26, R27, R28, R29: 10k; R_0603_1608Metric
R21, R22: 22; R_0603_1608Metric
R23, R24: 5.1K; R_0603_1608Metric
R30: 200; R_0603_1608Metric
SW1, SW2: SW_Push; SW_SPST_B3U-1000P-B
U1, U3: HX711; SOIC-16_3.9x9.9mm_P1.27mm
U4: STM32F103C8Tx; LQFP-48_7x7mm_P0.5mm
U5: LM3940IMP-3.3/NOPB; SOT-223
Y1: 8Mhz; Resonator_SMD_Murata_CSTxExxV-3Pin_3.0x1.1mm

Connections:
+3.3V: C7.1, C9.1, C16.2, C17.2, C18.2, C19.1, C21.1, J9.3 (VCC), Q1.2 (E), Q3.2 (E), R20.1, R25.1, R26.1, R27.1, R28.1, R29.1, R33.2, U1.1 (V_{SUP}), U1.15 (RATE), U1.16 (DV_{DD}), U3.1 (V_{SUP}), U3.15 (RATE), U3.16 (DV_{DD}), U4.9 (VDDA), U4.24 (VDD), U4.36 (VDD), U4.48 (VDD), U5.3 (OUT)
+5V: C20.1, J7.2, J10.A4 (VBUS), J10.A9 (VBUS), J10.B4 (VBUS), J10.B9 (VBUS), R30.1, R31.1, U5.1 (IN)
/D+: R22.1, U4.33 (PA12)
/D-: R21.1, U4.32 (PA11)
/E+_{LC1&2}: C11.1, J1.3, J3.3, Q1.3 (C), R14.1, U1.3 (AV_{DD})
/E+_{LC3&4}: C15.1, J5.3, Q3.3 (C), R18.1, U3.3 (AV_{DD})
/Programming_{RX}: J9.13 (VCP_RX), U4.13 (PA3)
/Programming_{TX}: J9.14 (VCP_TX), U4.12 (PA2)
/S+_{LC1}: J1.2, R1.1
/S+_{LC2}: J3.2, R3.1
/S+_{LC3}: J5.2, R9.1
/S-_{LC1}: J1.1, R2.1
/S-_{LC2}: J3.1, R4.1
/S-_{LC3}: J5.1, R10.1
/Trans1: Q4.1 (G), U4.22 (PB11)
/Trans2: Q5.1 (G), U4.25 (PB12)
/Trans3: Q6.1 (G), U4.26 (PB13)
/Trans4: Q7.1 (G), U4.27 (PB14)
/Trans5: Q8.1 (G), U4.28 (PB15)
/button1: J8.5, R25.2, U4.10 (PA0)
/button2: J8.4, R26.2, U4.11 (PA1)
/button3: J8.3, R27.2, U4.14 (PA4)
/button4: J8.2, R28.2, U4.15 (PA5)
/button5: J8.1, R29.2, U4.16 (PA6)
/codeclk: J9.6 (JCLK/SWCLK), U4.37 (PA14)
/codeio: J9.4 (JTMS/SWDIO), U4.34 (PA13)
/d+: J10.A6 (D+), J10.B6 (D+), R22.2
/d-: J10.A7 (D-), J10.B7 (D-), R21.2
/mcureset: J9.12 (~RST), R20.2, SW1.2, U4.7 (NRST)
GND: C7.2, C9.2, C10.2, C11.2, C14.2, C15.2, C16.1, C17.1, C18.1, C19.2, C20.2, C21.2, D1.1 (K), D2.1 (K), D3.1 (K), J1.4, J3.4, J5.4, J7.1, J9.5 (GND), J9.7 (GND), J9.11 (GNDDetect), J10.A1 (GND), J10.A12 (GND), J10.B1 (GND), J10.B12 (GND), Q4.2 (S), Q5.2 (S), Q6.2 (S), Q7.2 (S), Q8.2 (S), R13.2, R17.2, R23.1, R24.1, SW1.1, U1.5 (GND), U1.14 (XI), U3.5 (GND), U3.14 (XI), U4.8 (VSSA), U4.20 (PB2), U4.23 (VSS), U4.35 (VSS), U4.44 (BOOT0), U4.47 (VSS), U5.2 (GND), U5.4 (GND), Y1.2
unnamed: D1.2 (A), R30.2
unnamed: D2.2 (A), R31.2
unnamed: D3.2 (A), R32.2
unnamed: J10.A5 (CC1), R23.2
unnamed: J10.B5 (CC2), R24.2
unnamed: J11.1, Q4.3 (D)
unnamed: J11.2, Q5.3 (D)
unnamed: J11.3, Q6.3 (D)
unnamed: J11.4, Q7.3 (D)
unnamed: J11.5, Q8.3 (D)
unnamed: Q1.1 (B), U1.2 (BASE)
unnamed: Q3.1 (B), U3.2 (BASE)
unnamed: R33.1, SW2.2
unnamed: R13.1, R14.2, U1.4 (A_{FB})
unnamed: C2.1, R3.2, U1.8 (IN_{A+})
unnamed: C2.2, R4.2, U1.7 (IN_{A-})
unnamed: C1.1, R1.2, U1.10 (IN_{B+})
unnamed: C1.2, R2.2, U1.9 (IN_{B-})
unnamed: C10.1, U1.6 (V_{BG})
unnamed: R17.1, R18.2, U3.4 (A_{FB})
unnamed: C5.1, R9.2, U3.10 (IN_{B+})
unnamed: C5.2, R10.2, U3.9 (IN_{B-})
unnamed: C14.1, U3.6 (V_{BG})
unnamed: R32.1, U4.17 (PA7)
unnamed: SW2.1, U4.29 (PA8)
unnamed: U4.5 (PD0), Y1.1
unnamed: U4.6 (PD1), Y1.3
SCL: J7.4, U4.42 (PB6)
SDA: J7.3, U4.43 (PB7)
clk-shear: U4.41 (PB5)
clk-xforce: U1.11 (PD/SCK), U4.19 (PB1)
clk-yforce: U3.11 (PD/SCK), U4.46 (PB9)
dout-shear: U4.40 (PB4)
dout-xforce: U1.12 (DOUT), U4.18 (PB0)
dout-yforce: U3.12 (DOUT), U4.45 (PB8)

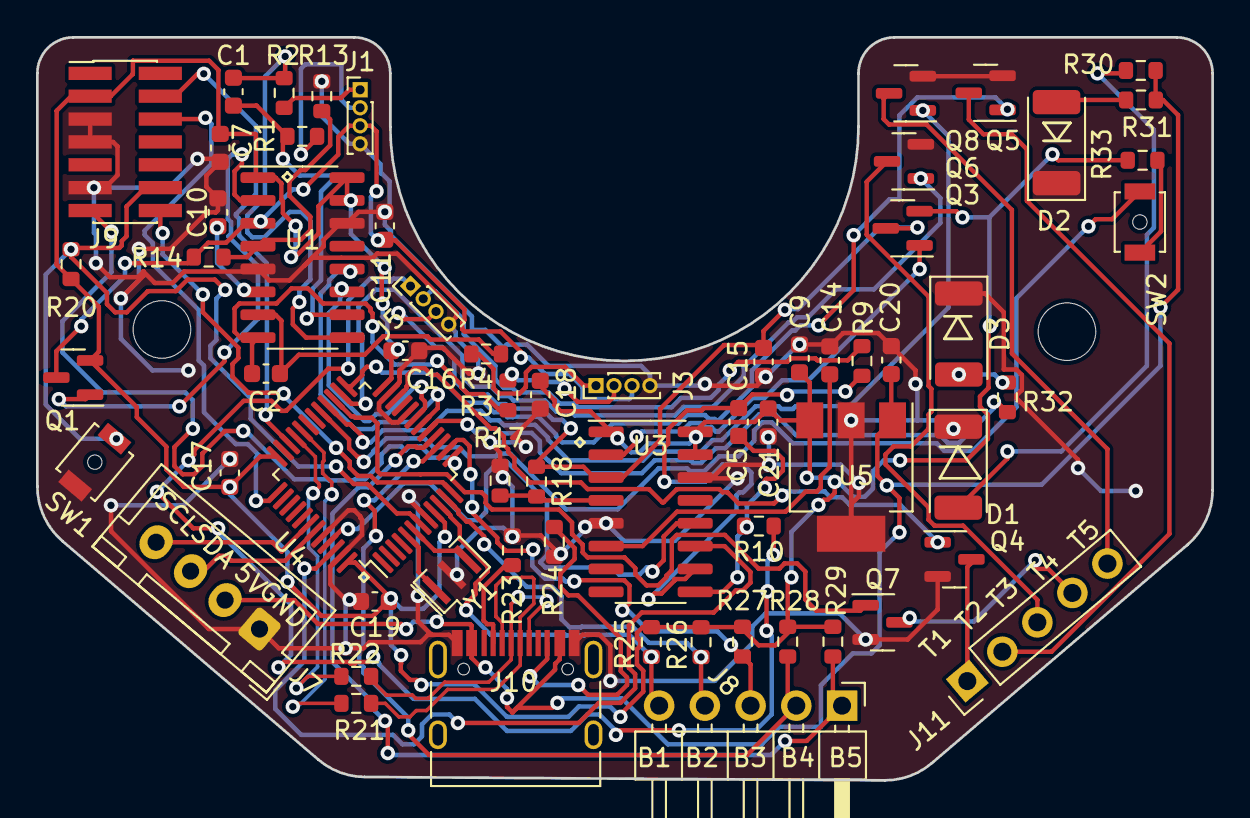
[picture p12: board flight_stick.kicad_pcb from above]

Board: 2 copper layers, 65.3 x 41.3 mm, 66 parts (0 on the bottom side), 63 nets.

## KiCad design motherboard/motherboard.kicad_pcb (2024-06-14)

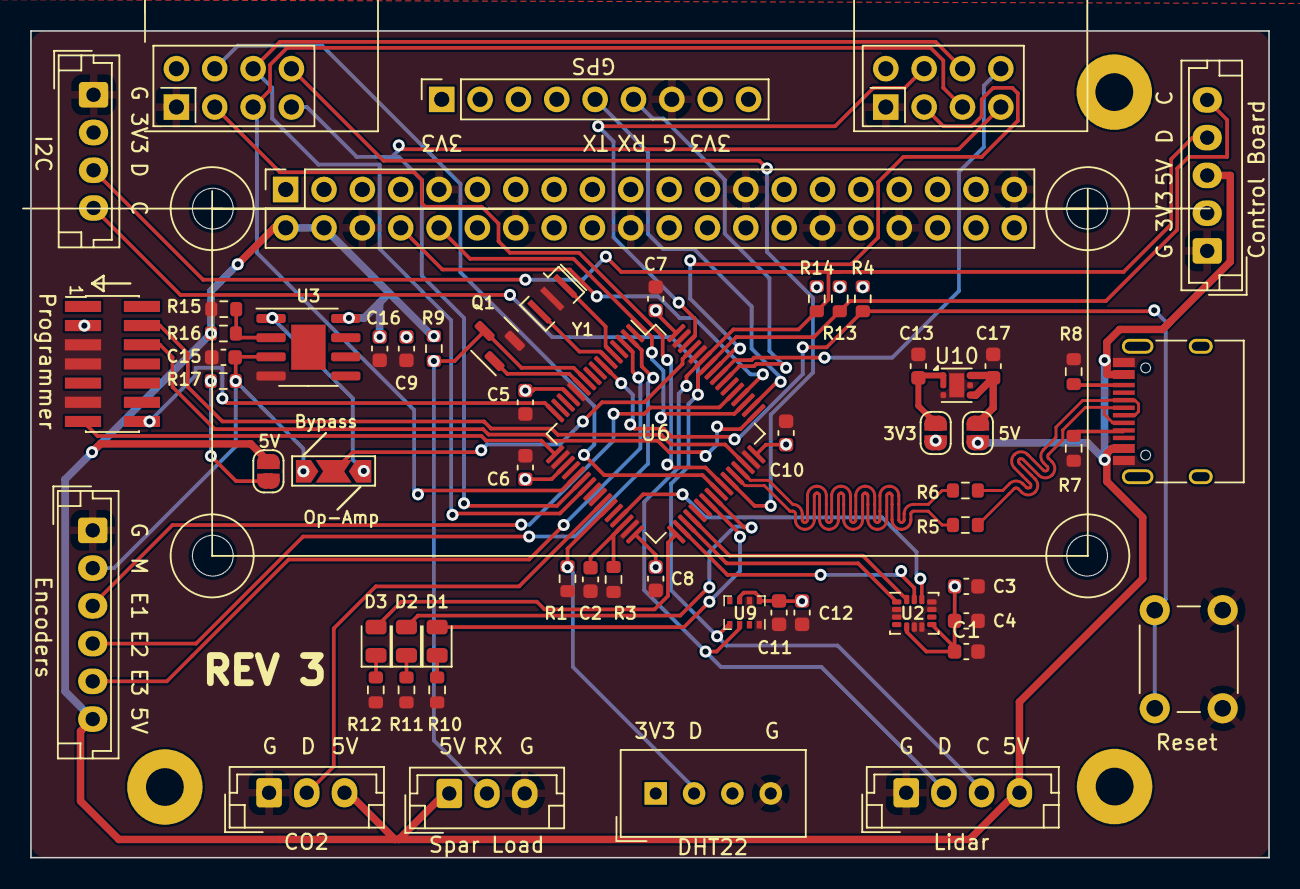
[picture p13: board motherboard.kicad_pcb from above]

Board: 2 copper layers, 82.0 x 54.8 mm, 67 parts (0 on the bottom side), 56 nets.

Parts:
C1, C9, C15: 10n; C_0603_1608Metric
C2: 4.7u; C_0603_1608Metric
C3: 2.2u; C_0603_1608Metric
C4, C5, C6, C7, C8, C11, C12, C16: 100n; C_0603_1608Metric
C10: 1u; C_0603_1608Metric
C13, C17: 0.22u; C_0603_1608Metric
D1, D2, D3: LED; LED_0805_2012Metric
H1, H3, H4: MountingHole; MountingHole_2.5mm_Pad
H5, H6, H7, H8: MountingHole; MountingHole_2.7mm_M2.5
J1: Raspberry_Pi_2_3 ANT; PinSocket_2x20_P2.54mm_Vertical
J2: Conn_ST_STDC14; PinHeader_2x07_P1.27mm_Vertical_SMD
J3: Battery / Pitot/ Orientation; JST_EH_B4B-EH-A_1x04_P2.50mm_Vertical
J4: c02 censor; JST_EH_B3B-EH-A_1x03_P2.50mm_Vertical
J5: shaftencorder; JST_EH_B6B-EH-A_1x06_P2.50mm_Vertical
J6: USB_C_Receptacle_USB2.0; USB_C_Receptacle_HRO_TYPE-C-31-M-12
J7: SparLoad; JST_EH_B3B-EH-A_1x03_P2.50mm_Vertical
J8: lidar; JST_EH_B4B-EH-A_1x04_P2.50mm_Vertical
J9: Control Board; JST_EH_B5B-EH-A_1x05_P2.50mm_Vertical
JP1: Jumper_3_Open; SolderJumper-3_P2.0mm_Open_TrianglePad1.0x1.5mm_NumberLabels
JP4: 5V; SolderJumper-2_P1.3mm_Open_RoundedPad1.0x1.5mm
JP5, JP6: Jumper_2_Open; SolderJumper-2_P1.3mm_Open_RoundedPad1.0x1.5mm
Q1: 2N7002K; SOT-23
R1, R3: 100k; R_0603_1608Metric
R4, R13, R14: 10k; R_0603_1608Metric
R5, R6: 22R; R_0603_1608Metric
R7, R8: 5.1K; R_0603_1608Metric
R9: 5.6k; R_0603_1608Metric
R10, R11, R12: 130R; R_0603_1608Metric
R15: 1k; R_0603_1608Metric
R16: 20k; R_0603_1608Metric
R17: 470R; R_0603_1608Metric
SW1: MCU_RST; SW_PUSH_6mm_H4.3mm
U2: IMU; LGA-14_3x2.5mm_P0.5mm_LayoutBorder3x4y
U3: LM358; SOIC-8-1EP_3.9x4.9mm_P1.27mm_EP2.29x3mm
U4: GPS module; PinSocket_1x09_P2.54mm_Vertical
U5: DHT11(DHT22); Aosong_DHT11_5.5x12.0_P2.54mm
U6: STM32F412RETx; LQFP-64_10x10mm_P0.5mm
U7: nRF24L01-telemetry-INTERIOR; nRF24L01_Breakout
U8: nRF24L01-telemetry-EXTERIOR; nRF24L01_Breakout
U9: DPS310 - barometer; Bosch_LGA-8_2x2.5mm_P0.65mm_ClockwisePinNumbering
U10: TLV76733DRVx; WSON-6-1EP_2x2mm_P0.65mm_EP1x1.6mm
Y1: 8M; Resonator_SMD_Murata_CSTxExxV-3Pin_3.0x1.1mm

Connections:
+3.3V: C1.1, C3.1, C4.1, C5.2, C6.2, C7.2, C8.2, C9.2, C10.2, C11.1, C12.1, J2.3 (VCC), J3.2, J9.2, JP5.2 (B), R4.2, R13.1, R14.1, U2.5 (VDD_{IO}), U2.8 (VDD), U4.1 (3.3V), U4.8 (VIN), U5.1 (VDD), U6.13 (VDDA), U6.19 (VDD), U6.32 (VDD), U6.48 (VDD), U6.64 (VDD), U7.2 (VCC), U8.2 (VCC), U9.6 (V_{DDIO}), U9.8 (V_{DD})
+5V: C16.1, J1.2 (5V), J1.4 (5V), J4.3, J5.6, J6.A4 (VBUS), J6.A9 (VBUS), J6.B4 (VBUS), J6.B9 (VBUS), J7.1, J8.4, J9.3, JP4.2 (B), JP6.1 (A), R9.1, R16.1, U3.8 (V+)
/CO_{2}: J4.2, U6.26 (PB0)
/D+: J6.A6 (D+), J6.B6 (D+), R6.2
/D-: J6.A7 (D-), J6.B7 (D-), R5.2
/DHT22: R1.2, U5.2 (DATA), U6.27 (PB1)
/ENC1: J5.3, U6.53 (PC12)
/ENC2: J5.4, U6.2 (PC13)
/ENC3: J5.5, U6.3 (PC14)
/I2C_{SCK}: J3.4, J8.3, J9.5, R13.2, U6.58 (PB6), U9.4 (SCK)
/I2C_{SDA}: J3.3, J8.2, J9.4, R14.2, U6.59 (PB7), U9.3 (SDI)
/IMU_{CS}: U2.12 (CS), U6.29 (PB10)
/LED1: D1.2 (A), U6.39 (PC8)
/LED2: D2.2 (A), U6.40 (PC9)
/LED3: D3.2 (A), U6.33 (PB12)
/OneWire_{RX}: J7.2, Q1.3 (D), R9.2, U6.10 (PC2)
/OneWire_{TX}: Q1.1 (G), U6.11 (PC3)
/RST: R4.1, SW1.2, U6.7 (NRST)
/SHAFTENC IN: C15.1, J5.2, JP1.1 (A), R17.2, U3.3 (+)
/SHAFTENC OUT: JP1.2 (C), U6.61 (PB8)
/SPI1MISO: U6.22 (PA6), U7.7 (MISO), U8.7 (MISO)
/SPI1MOSI: U6.23 (PA7), U7.6 (MOSI), U8.6 (MOSI)
/SPI1SCK: U6.21 (PA5), U7.5 (SCK), U8.5 (SCK)
/SPI2MISO: U2.1 (SDO), U6.35 (PB14)
/SPI2MOSI: U2.14 (SDI), U6.36 (PB15)
/SPI2SCK: U2.13 (SCK), U6.34 (PB13)
/SWCLK: J2.6 (JCLK/SWCLK), U6.49 (PA14)
/SWDIO: J2.4 (JTMS/SWDIO), U6.46 (PA13)
/TELE_{CE}-E: U6.42 (PA9), U8.3 (CE)
/TELE_{CE}-int: U6.57 (PB5), U7.3 (CE)
/TELE_{CS}-E: U6.41 (PA8), U8.4 (~CSN)
/TELE_{CS}-int: U6.62 (PB9), U7.4 (~CSN)
/TELE_{IRQ}-E: U6.43 (PA10), U8.8 (IRQ)
/TELE_{IRQ}-int: U6.56 (PB4), U7.8 (IRQ)
/USART1_{RX}: U4.6 (RX), U6.55 (PB3)
/USART1_{TX}: U4.5 (TX), U6.50 (PA15)
/USART2_{RX}: J2.13 (VCP_RX), U6.17 (PA3)
/USART2_{TX}: J2.14 (VCP_TX), U6.16 (PA2)
/USART3_{RX}: J1.8 (GPIO14/TXD), U6.52 (PC11)
/USART3_{TX}: J1.10 (GPIO15/RXD), U6.51 (PC10)
/USB+: R6.1, U6.45 (PA12)
/USB-: R5.1, U6.44 (PA11)
GND: C1.2, C2.2, C3.2, C4.2, C5.1, C6.1, C7.1, C8.1, C9.1, C10.1, C11.2, C12.2, C13.2, C15.2, C16.2, C17.2, J1.6 (GND), J1.9 (GND), J1.14 (GND), J1.20 (GND), J1.25 (GND), J1.30 (GND), J1.34 (GND), J1.39 (GND), J2.5 (GND), J2.7 (GND), J2.11 (GNDDetect), J3.1, J4.1, J5.1, J6.A1 (GND), J6.A12 (GND), J6.B1 (GND), J6.B12 (GND), J7.3, J8.1, J9.1, Q1.2 (S), R1.1, R3.1, R7.1, R8.1, R10.1, R11.1, R12.2, R15.2, SW1.1, U2.2 (RESV), U2.3 (RESV), U2.6 (GND), U2.7 (RESV), U2.10 (RESV), U2.11 (RESV), U3.4 (V-), U4.7 (GND), U5.4 (GND), U6.12 (VSSA), U6.18 (VSS), U6.31 (VSS), U6.47 (VSS), U6.60 (BOOT0), U6.63 (VSS), U7.1 (GND), U8.1 (GND), U9.1 (GND), U9.7 (GND), U10.3 (GND), U10.5 (GND), U10.7 (PAD), Y1.2
unnamed: D1.1 (K), R10.2
unnamed: D2.1 (K), R11.2
unnamed: D3.1 (K), R12.1
unnamed: J6.A5 (CC1), R7.2
unnamed: J6.B5 (CC2), R8.2
unnamed: JP1.3 (B), U3.1
unnamed: JP4.1 (A), R17.1
unnamed: C13.1, JP5.1 (A), U10.1 (OUT), U10.2 (SNS)
unnamed: C17.1, JP6.2 (B), U10.4 (EN), U10.6 (IN)
unnamed: R15.1, R16.2, U3.2 (-)
unnamed: U6.5 (PH0), Y1.1
unnamed: U6.6 (PH1), Y1.3
unnamed: C2.1, R3.2, U6.30 (VCAP_1)

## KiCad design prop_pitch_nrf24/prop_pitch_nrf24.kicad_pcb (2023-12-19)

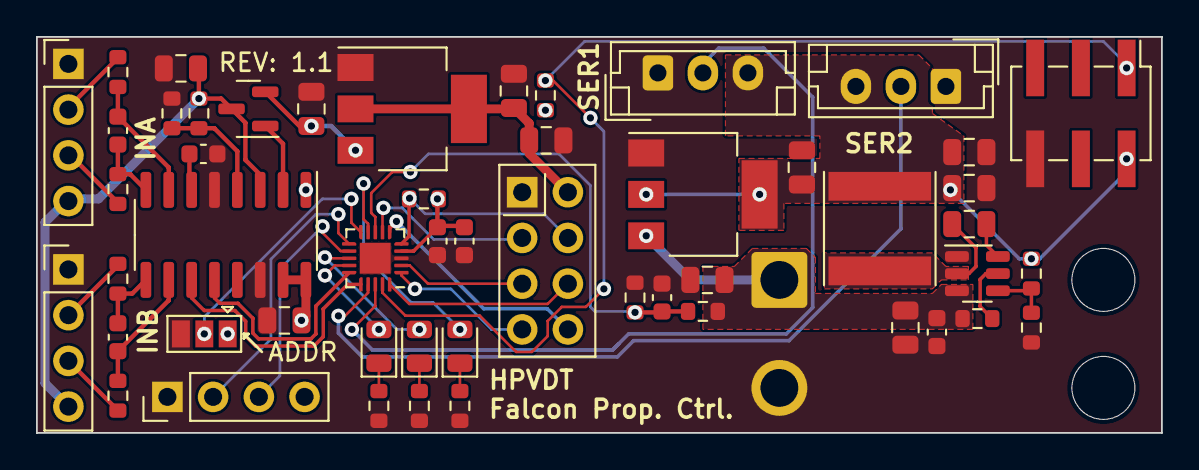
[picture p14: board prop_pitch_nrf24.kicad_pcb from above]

Board: 2 copper layers, 62.5 x 22.0 mm, 53 parts (1 on the bottom side), 41 nets.

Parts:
BT1: Battery; SolderWire-1.5sqmm_1x02_P6mm_D1.7mm_OD3mm_Relief
C1, C2, C3, C5, C9, C11: 100n; C_0603_1608Metric
C4, C6, C10, C15, C16, C18: 10u; C_0805_2012Metric
C7: 10n; C_0603_1608Metric
C12: 100n; C_0805_2012Metric
C13, C14, C19, C20: 22u; C_0805_2012Metric
D1, D2, D3: LED; LED_0805_2012Metric
J1: LOAD1; PinHeader_1x04_P2.54mm_Vertical
J2: LOAD2; PinHeader_1x04_P2.54mm_Vertical
J3: AVR-UPDI-6; PinHeader_2x03_P2.54mm_Vertical_SMD
J4: SERVO2; JST_EH_B3B-EH-A_1x03_P2.50mm_Vertical
J5: SERVO1; JST_EH_B3B-EH-A_1x03_P2.50mm_Vertical
J6: SERIAL; PinHeader_1x04_P2.54mm_Vertical
JP1: ADDRESS; SolderJumper-3_P1.3mm_Open_Pad1.0x1.5mm
L1: 3u3; L_Taiyo-Yuden_NR-60xx
Q1: MMSS8550; SOT-23
R1, R2, R3: 430; R_0603_1608Metric
R4, R5, R6, R7: 100; R_0603_1608Metric
R8: 15k; R_0603_1608Metric
R9, R12, R13, R14, R16: 10k; R_0603_1608Metric
R10: 20k; R_0603_1608Metric
R11: 8.2k; R_0603_1608Metric
R15: 54k9; R_0603_1608Metric
U1: ATtiny1616-M; VQFN-20-1EP_3x3mm_P0.4mm_EP1.7x1.7mm
U2: HX711; SOP-16_3.9x9.9mm_P1.27mm
U3: TPS563208DDCR; TSOT-23-6
U4: AZ1117-5.0; SOT-223-3_TabPin2
U5: AZ1117-3.3; SOT-223-3_TabPin2
U6: NRF24L01_Breakout; nRF24L01_Breakout

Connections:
+3.3VA: C6.2, J1.4, J2.4, Q1.3 (C), R10.1, U2.3 (AVDD)
+3V3: C18.2, C20.2, U5.2 (VO), U6.2 (VCC)
+5V: C4.2, C5.1, C7.1, C13.2, C14.2, C16.2, C19.2, J3.2 (VCC), J4.3, J5.3, J6.4, JP1.1 (A), L1.2, Q1.2 (E), R12.1, R13.1, R15.1, U1.4 (VCC), U2.1 (VSUP), U2.15 (RATE), U2.16 (DVDD), U4.2 (VO), U5.3 (VI)
+BATT: BT1.1 (+), C10.2, C11.2, C15.2, R8.1, R14.1, U3.3 (VIN), U4.3 (VI)
/ADDRESS: JP1.2 (C), U1.10 (PB4)
/BASE: Q1.1 (B), U2.2 (BASE)
/BATT_{SCALED}: C3.1, R8.2, R9.1, U1.8 (PA7)
/CE_{nRF}: U1.7 (PA6), U6.3 (CE)
/DOUT_{AMP}: U1.15 (PC0), U2.12 (DOUT)
/FB: R15.2, R16.2, U3.4 (VFB)
/FB_{VA}: R10.2, R11.1, U2.4 (VFB)
/INA+: C1.2, R4.2, U2.8 (INA+)
/INA-: C1.1, R5.2, U2.7 (INA-)
/INB+: C2.2, R6.2, U2.10 (INB+)
/INB-: C2.1, R7.2, U2.9 (INB-)
/INT_{nRF}: U1.6 (PA5), U6.8 (IRQ)
/LED_{1}: D1.2 (A), U1.14 (PB0)
/LED_{2}: D2.2 (A), U1.13 (PB1)
/LED_{3}: D3.2 (A), U1.9 (PB5)
/MISO: U1.1 (PA2), U6.7 (MISO)
/MOSI: U1.20 (PA1), U6.6 (MOSI)
/RX: J6.2, U1.11 (PB3)
/S+_{LC1}: J1.3, R4.1
/S+_{LC2}: J2.3, R6.1
/S-_{LC1}: J1.2, R5.1
/S-_{LC2}: J2.2, R7.1
/SCK: U1.2 (PA3), U6.5 (SCK)
/SCK_{AMP}: U1.16 (PC1), U2.11 (PD_SCK)
/SERVO_{1}: J5.2, U1.18 (PC3)
/SERVO_{2}: J4.2, U1.17 (PC2)
/TX: J6.3, U1.12 (PB2)
/~CS_{nRF}: R13.2, U1.5 (PA4), U6.4 (~CSN)
/~RESET: J3.1 (DATA), R12.2, U1.19 (~RESET/PA0)
GND: BT1.2 (-), C3.2, C4.1, C5.2, C6.1, C7.2, C9.1, C10.1, C11.1, C13.1, C14.1, C15.1, C16.1, C18.1, C19.1, C20.1, J1.1, J2.1, J3.6 (GND), J4.1, J5.1, J6.1, JP1.3 (B), R1.2, R2.2, R3.2, R9.2, R11.2, R16.1, U1.3 (GND), U1.21 (GND), U2.5 (AGND), U2.14 (XI), U3.1 (GND), U4.1 (GND), U5.1 (GND), U6.1 (GND)
unnamed: D1.1 (K), R1.1
unnamed: D2.1 (K), R2.1
unnamed: D3.1 (K), R3.1
unnamed: C9.2, U2.6 (VBG)
unnamed: R14.2, U3.5 (EN)
unnamed: C12.2, L1.1, U3.2 (SW)
unnamed: C12.1, U3.6 (VBST)

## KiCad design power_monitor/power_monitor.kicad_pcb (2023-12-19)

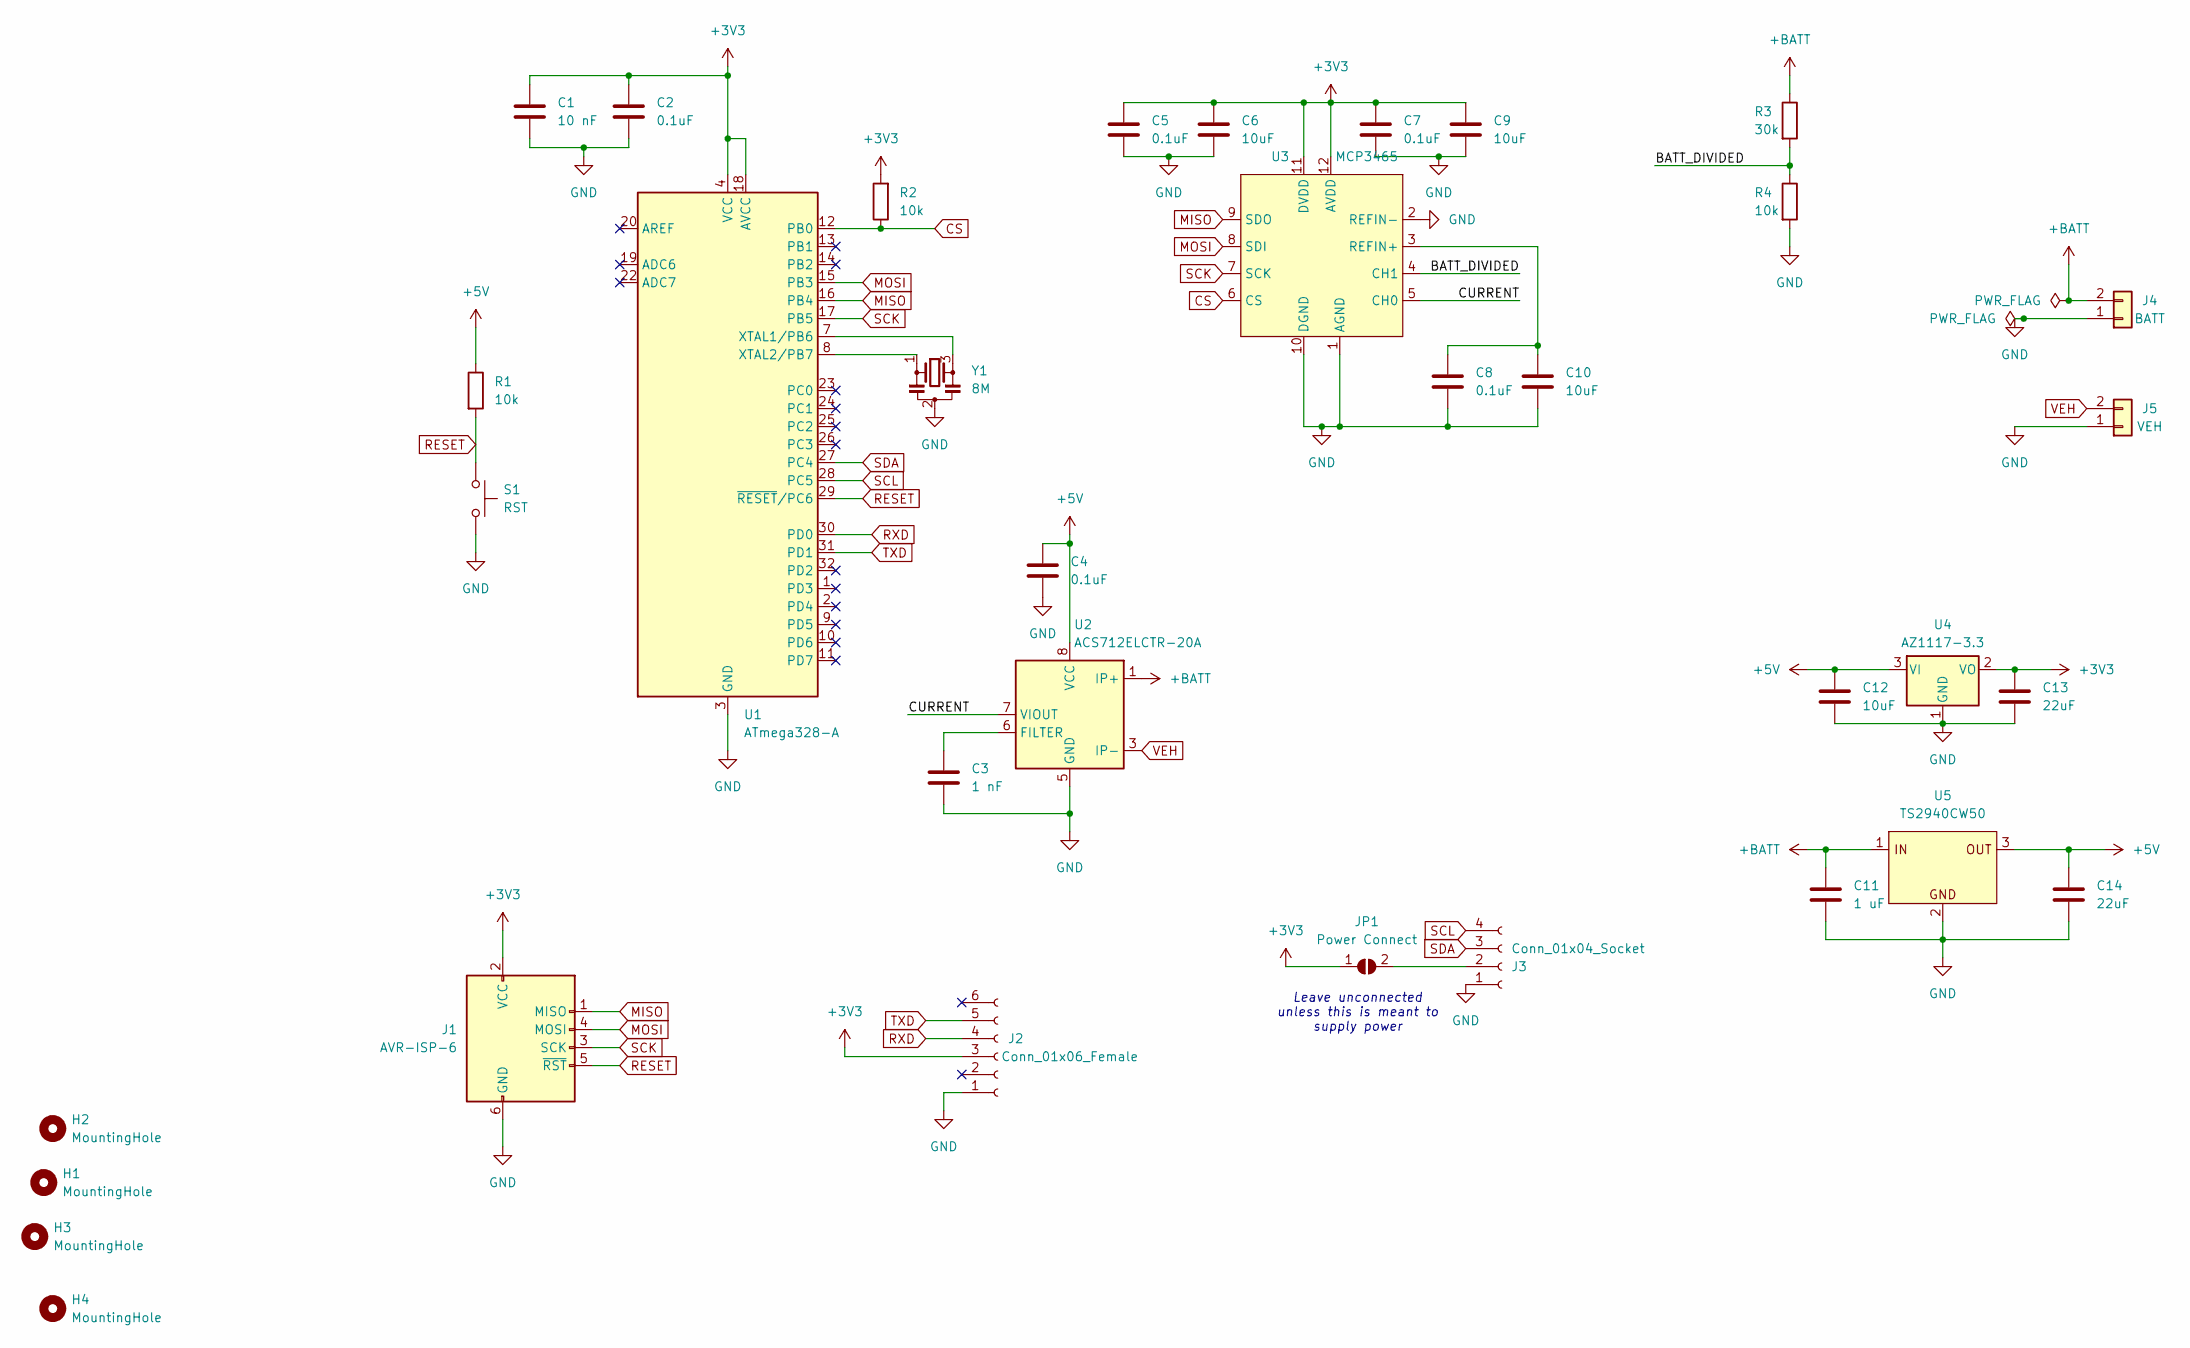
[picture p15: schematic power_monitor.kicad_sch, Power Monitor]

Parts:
C1: 10 nF; C_0603_1608Metric
C2, C4, C5, C7, C8: 0.1uF; C_0603_1608Metric
C3: 1 nF; C_0603_1608Metric
C6, C9, C10, C12: 10uF; C_0805_2012Metric
C11: 1 uF; C_0603_1608Metric
C13, C14: 22uF; C_0805_2012Metric
H1, H2, H3, H4: MountingHole; MountingHole_3.2mm_M3_ISO14580
J1: AVR-ISP-6; PinHeader_2x03_P2.54mm_Vertical_SMD
J2: Conn_01x06_Female; PinHeader_1x06_P2.54mm_Vertical
J3: Conn_01x04_Socket; JST_XA_B04B-XASK-1_1x04_P2.50mm_Vertical
J4: BATT; AMASS_XT60-M_1x02_P7.20mm_Vertical
J5: VEH; AMASS_XT60-F_1x02_P7.20mm_Vertical
JP1: Power Connect; SolderJumper-2_P1.3mm_Open_Pad1.0x1.5mm
R1, R2, R4: 10k; R_0603_1608Metric
R3: 30k; R_0603_1608Metric
S1: RST; SW_SPST_SKQG_WithStem
U1: ATmega328-A; TQFP-32_7x7mm_P0.8mm
U2: ACS712ELCTR-20A; SOIC-8_3.9x4.9mm_P1.27mm
U3: MCP3465; QFN-12_EP_2x2_Pitch0.4mm
U4: AZ1117-3.3; SOT-223-3_TabPin2
U5: TS2940CW50; SOT-223-3_TabPin2
Y1: 8M; Resonator_SMD_Murata_CSTxExxV-3Pin_3.0x1.1mm

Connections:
+3V3: C1.1, C2.1, C5.1, C6.1, C7.1, C9.1, C13.1, J1.2 (VCC), J2.3, JP1.1 (A), R2.2, U1.4 (VCC), U1.6 (VCC), U1.18 (AVCC), U3.11 (DVDD), U3.12 (AVDD), U4.2 (VO)
+5V: C4.1, C12.1, C14.1, R1.1, U2.8 (VCC), U4.3 (VI), U5.3
+BATT: C11.1, J4.2, R3.1, U2.1 (IP+), U2.2 (IP+), U5.1
/BATT_DIVIDED: R3.2, R4.1, U3.4 (CH1)
/CURRENT: U2.7 (VIOUT), U3.5 (CH0)
CS: R2.1, U1.12 (PB0), U3.6 (CS)
GND: C1.2, C2.2, C3.2, C4.2, C5.2, C6.2, C7.2, C8.2, C9.2, C10.2, C11.2, C12.2, C13.2, C14.2, J1.6 (GND), J2.1, J3.1, J4.1, J5.1, R4.2, S1.2, U1.3 (GND), U1.5 (GND), U1.21 (GND), U2.5 (GND), U3.1 (AGND), U3.2 (REFIN-), U3.10 (DGND), U3.13 (EP), U4.1 (GND), U5.2, Y1.2
MISO: J1.1 (MISO), U1.16 (PB4), U3.9 (SDO)
MOSI: J1.4 (MOSI), U1.15 (PB3), U3.8 (SDI)
unnamed: J3.2, JP1.2 (B)
unnamed: U1.7 (XTAL1/PB6), Y1.3
unnamed: U1.8 (XTAL2/PB7), Y1.1
unnamed: C3.1, U2.6 (FILTER)
unnamed: C8.1, C10.1, U3.3 (REFIN+)
RESET: J1.5 (~RST), R1.2, S1.1, U1.29 (~RESET/PC6)
RXD: J2.4, U1.30 (PD0)
SCK: J1.3 (SCK), U1.17 (PB5), U3.7 (SCK)
SCL: J3.4, U1.28 (PC5)
SDA: J3.3, U1.27 (PC4)
TXD: J2.5, U1.31 (PD1)
VEH: J5.2, U2.3 (IP-), U2.4 (IP-)

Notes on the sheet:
Leave unconnected unless this is meant to supply power

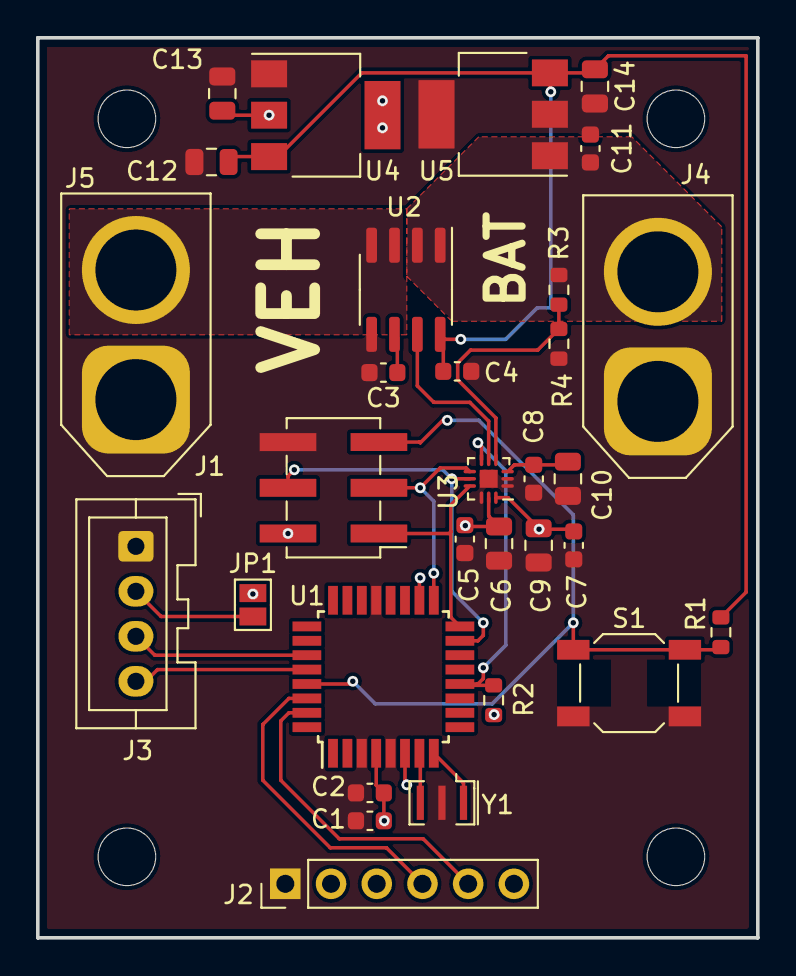
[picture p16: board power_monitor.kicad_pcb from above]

Board: 2 copper layers, 40.0 x 50.0 mm, 35 parts (0 on the bottom side), 21 nets.

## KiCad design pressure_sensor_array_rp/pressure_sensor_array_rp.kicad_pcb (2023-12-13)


Board: 2 copper layers, 99.0 x 60.0 mm, 44 parts (0 on the bottom side), 38 nets.

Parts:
C1, C2, C3, C4, C5, C6, C7, C14, C16: 100n; C_0603_1608Metric
C8, C9: 22u; C_0603_1608Metric
C12, C15: 1n; C_0603_1608Metric
C17, C18: 27p; C_0603_1608Metric
H1, H2, H3: MountingHole; MountingHole_3.2mm_M3
J1: Conn_01x04_Pin; PinHeader_1x04_P2.54mm_Vertical
J2: USB_C_Receptacle_USB2.0; USB_C_Receptacle_HRO_TYPE-C-31-M-12
J3: Conn_01x06_Pin; PinHeader_1x06_P2.54mm_Vertical
J5: Conn_01x03_Pin; JST_EH_B3B-EH-A_1x03_P2.50mm_Vertical
R1, R2, R3, R4, R5, R6: 10k; R_0603_1608Metric
R7, R8: 1k; R_0603_1608Metric
R9, R10: 5.1k; R_0603_1608Metric
R11, R12: 22; R_0603_1608Metric
SW1: Reset; SW_SPST_SKQG_WithStem
SW2: Boot Mode; SW_SPST_SKQG_WithStem
U1, U2, U3, U4: HV120SM02C
U5: W25Q128JVS; SOIC-8_5.23x5.23mm_P1.27mm
U6: RP2040; QFN-56-1EP_7x7mm_P0.4mm_EP3.2x3.2mm
U7: AZ1117-3.3; SOT-223-3_TabPin2
Y1: Crystal; Crystal_SMD_HC49-SD(ABLS-12.000MHZ-B4-T)

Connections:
+1V1: C14.1, C15.1, U6.23 (DVDD), U6.45 (VREG_VOUT), U6.50 (DVDD)
+3.3V: C1.1, C2.1, C3.1, C4.1, C5.1, C6.1, C7.1, C8.2, C12.1, C16.1, J1.2, J3.3, R1.2, R2.2, R3.2, R4.2, R5.1, R6.1, U1.9 (VDD), U2.9 (VDD), U3.9 (VDD), U4.9 (VDD), U5.8 (VCC), U6.1 (IOVDD), U6.10 (IOVDD), U6.22 (IOVDD), U6.33 (IOVDD), U6.42 (IOVDD), U6.43 (ADC_AVDD), U6.44 (VREG_IN), U6.48 (USB_VDD), U6.49 (IOVDD), U7.2 (VO)
+5V: C9.2, J2.A4 (VBUS), J2.A9 (VBUS), J2.B4 (VBUS), J2.B9 (VBUS), U7.3 (VI)
/D+: J2.A6 (D+), J2.B6 (D+), R12.1
/D-: J2.A7 (D-), J2.B7 (D-), R11.1
/DAV_{1}: U1.11 (DAV), U6.17 (GPIO14)
/DAV_{2}: U2.11 (DAV), U6.18 (GPIO15)
/DAV_{3}: U3.11 (DAV), U6.27 (GPIO16)
/DAV_{4}: U4.11 (DAV), U6.29 (GPIO18)
/MISO: U1.3 (MISO), U2.3 (MISO), U3.3 (MISO), U4.3 (MISO), U6.6 (GPIO4)
/MOSI: U1.2 (MOSI), U2.2 (MOSI), U3.2 (MOSI), U4.2 (MOSI), U6.9 (GPIO7)
/QSPI_SCLK: U5.6 (CLK), U6.52 (QSPI_SCLK)
/QSPI_SD0: U5.5 (DI(IO0)), U6.53 (QSPI_SD0)
/QSPI_SD1: U5.2 (DO(IO1)), U6.55 (QSPI_SD1)
/QSPI_SD2: U5.3 (IO2), U6.54 (QSPI_SD2)
/QSPI_SD3: U5.7 (IO3), U6.51 (QSPI_SD3)
/QSPI_SS: R6.2, R7.1, U5.1 (~CS), U6.56 (QSPI_SS)
/RXD: J3.4, U6.3 (GPIO1)
/SCK: U1.4 (SCK), U2.4 (SCK), U3.4 (SCK), U4.4 (SCK), U6.8 (GPIO6)
/SCL: J1.4, U6.5 (GPIO3)
/SDA: J1.3, U6.4 (GPIO2)
/SWCLK: J5.3, U6.24 (SWCLK)
/SWD: J5.1, U6.25 (SWD)
/TXD: J3.5, U6.2 (GPIO0)
/USB_BOOT: R7.2, SW2.2
/USB_D+: R12.2, U6.47 (USB_DP)
/USB_D-: R11.2, U6.46 (USB_DM)
/nRST: R5.2, SW1.2, U1.10 (nRST), U2.10 (nRST), U3.10 (nRST), U4.10 (nRST), U6.26 (RUN)
/nSS_{1}: R1.1, U1.1 (nSS), U6.28 (GPIO17)
/nSS_{2}: R2.1, U2.1 (nSS), U6.7 (GPIO5)
/nSS_{3}: R3.1, U3.1 (nSS), U6.12 (GPIO9)
/nSS_{4}: R4.1, U4.1 (nSS), U6.16 (GPIO13)
GND: C1.2, C2.2, C3.2, C4.2, C5.2, C6.2, C7.2, C8.1, C9.1, C12.2, C14.2, C15.2, C16.2, C17.1, C18.1, J1.1, J2.A1 (GND), J2.A12 (GND), J2.B1 (GND), J2.B12 (GND), J3.1, J5.2, R9.2, R10.2, SW1.1, SW2.1, U1.8 (GND), U2.8 (GND), U3.8 (GND), U4.8 (GND), U5.4 (GND), U6.19 (TESTEN), U6.57 (GND), U7.1 (GND)
unnamed: C17.2, R8.1, Y1.1
unnamed: J2.A5 (CC1), R9.1
unnamed: J2.B5 (CC2), R10.1
unnamed: C18.2, U6.20 (XIN), Y1.2
unnamed: R8.2, U6.21 (XOUT)

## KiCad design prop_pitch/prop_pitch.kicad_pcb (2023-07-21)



Board: 2 copper layers, 65.0 x 22.0 mm, 54 parts (12 on the bottom side), 40 nets.

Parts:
BT1: Battery; SolderWire-1.5sqmm_1x02_P6mm_D1.7mm_OD3mm_Relief
C1, C5: 10n; C_0603_1608Metric
C2, C3, C4, C6, C7, C9, C18: 100n; C_0603_1608Metric
C8, C11, C12, C13, C14, C15: 22uF; C_0805_2012Metric
C10, C19, C20: 10u; C_0805_2012Metric
C16, C17: 100n; C_0805_2012Metric
D1, D2, D3: LED; LED_0805_2012Metric
J1: AVR-ISP-6; IDC-Header_2x03_P2.54mm_Vertical_SMD
J2: LOAD1; PinHeader_1x04_P2.54mm_Vertical
J3: LOAD2; PinHeader_1x04_P2.54mm_Vertical
J4: SERVO1; JST_EH_B3B-EH-A_1x03_P2.50mm_Vertical
J6: SERVO2; JST_EH_B3B-EH-A_1x03_P2.50mm_Vertical
L1: 3.3uH; L_Taiyo-Yuden_NR-60xx
Q1: MMSS8550; SOT-23
R1, R3, R5, R12, R13: 10k; R_0603_1608Metric
R2: 15k; R_0603_1608Metric
R4: 5.1k; R_0603_1608Metric
R6, R7, R8, R9: 100; R_0603_1608Metric
R10: 20k; R_0603_1608Metric
R11: 8.2k; R_0603_1608Metric
R14: 54.9k; R_0603_1608Metric
R15, R16, R17: 430; R_0603_1608Metric
U1: ATmega328P-A; TQFP-32_7x7mm_P0.8mm
U3: HC-05; PinHeader_1x06_P2.54mm_Vertical
U4: TPS563208DDCR; TSOT-23-6
U5: AZ1117-5.0; SOT-223-3_TabPin2
U6: HX711; SOP-16_3.9x9.9mm_P1.27mm
Y1: 16M; Resonator_SMD_Murata_CSTxExxV-3Pin_3.0x1.1mm

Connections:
+3.3VA: C20.2, J2.4, J3.4, Q1.3 (C), R10.1, U6.3 (AVDD)
+5V: C1.1, C2.1, C8.2, C10.2, C11.2, C12.2, C17.2, C18.1, J1.2 (VCC), J4.3, J6.3, L1.1, Q1.2 (E), R1.1, R14.1, U1.4 (VCC), U1.6 (VCC), U1.18 (AVCC), U3.2 (VCC), U5.2 (VO), U6.1 (VSUP), U6.15 (RATE), U6.16 (DVDD)
+BATT: BT1.1 (+), C13.2, C14.2, C15.2, C19.2, R2.1, R13.2, U4.3 (VIN), U5.3 (VI)
/BASE: Q1.1 (B), U6.2 (BASE)
/BATT_{SCALED}: C3.1, R2.2, R3.1, U1.22 (ADC7)
/BST: C16.2, U4.6 (VBST)
/BT_{RX}: U1.31 (PD1), U3.5 (RX)
/BT_{TX}: R4.1, U1.30 (PD0)
/DOUT_{AMP}: U1.26 (PC3), U6.12 (DOUT)
/EN: R13.1, U4.5 (EN)
/FB_{VA}: R10.2, R11.1, U6.4 (VFB)
/INA+: C7.2, R9.2, U6.8 (INA+)
/INA-: C7.1, R8.2, U6.7 (INA-)
/INB+: C6.2, R7.2, U6.10 (INB+)
/INB-: C6.1, R6.2, U6.9 (INB-)
/LED_{1}: D1.2 (A), U1.1 (PD3)
/LED_{2}: D2.2 (A), U1.9 (PD5)
/LED_{3}: D3.2 (A), U1.10 (PD6)
/MISO: J1.1 (MISO), U1.16 (PB4)
/MOSI: J1.4 (MOSI), U1.15 (PB3)
/S+_{LC1}: J2.3, R9.1
/S+_{LC2}: J3.3, R7.1
/S-_{LC1}: J2.2, R8.1
/S-_{LC2}: J3.2, R6.1
/SCK: J1.3 (SCK), U1.17 (PB5)
/SCK_{AMP}: U1.27 (PC4), U6.11 (PD_SCK)
/SERVO_{1}: J4.2, U1.13 (PB1)
/SERVO_{2}: J6.2, U1.14 (PB2)
/SW: C16.1, L1.2, U4.2 (SW)
/VFB: C17.1, R12.2, R14.2, U4.4 (VFB)
/~RESET: C5.1, J1.5 (~RST), R1.2, U1.29 (~RESET/PC6)
GND: BT1.2 (-), C1.2, C2.2, C3.2, C4.2, C5.2, C8.1, C9.1, C10.1, C11.1, C12.1, C13.1, C14.1, C15.1, C18.2, C19.1, C20.1, J1.6 (GND), J2.1, J3.1, J4.1, J6.1, R3.2, R5.2, R11.2, R12.1, R15.2, R16.2, R17.2, U1.3 (GND), U1.5 (GND), U1.21 (GND), U3.3 (GND), U4.1 (GND), U5.1 (GND), U6.5 (AGND), U6.14 (XI), Y1.2
unnamed: D1.1 (K), R15.1
unnamed: D2.1 (K), R16.1
unnamed: D3.1 (K), R17.1
unnamed: C4.1, U1.20 (AREF)
unnamed: U1.7 (XTAL1/PB6), Y1.3
unnamed: U1.8 (XTAL2/PB7), Y1.1
unnamed: R4.2, R5.1, U3.4 (TX)
unnamed: C9.2, U6.6 (VBG)

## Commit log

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2023-07-12 Touched up spar sensor to reflect parts as ordered
    [spar_sensor.kicad_pcb, spar_sensor.kicad_sch]
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2023-08-03 Add files via upload
    I am so confused I'm not sure I ever understood how to understand this stuff :). Also never used GitHub bfr so hopefully this is the right way to share edits
    [power_monitor_EunGuRevision.kicad_sch]
2023-08-04 Finished schematic
    Updated with new ADC and added voltage regulator
    [power_monitor_EunGuRevision.kicad_sch]
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2023-08-08 PCB Arrangement
    uh Savo how do I do this. I just grouped everything that needed to be together but I didn't fully finish. Also I'll send it over discord in case this isn't the right one
    [power_monitor_EunGuRevision.kicad_pcb]
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2023-08-15 PCB Layout
    Created initial PCB layout and included more complicated connections to give an idea of what's going on. There's a connection that goes under the board since my brain does not know how to rearrange t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
    [power_monitor.kicad_pcb, power_monitor.kicad_sch]
2023-08-18 PCB Layout finished
    HAHAHAHAHA IT'S DONE. will commence routing.
    [power_monitor.kicad_pcb, power_monitor.kicad_sch]
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2023-08-18 Preliminary routing
    Rough ideas for routing. Didn't do any ground connections yet.
    [power_monitor.kicad_pcb]
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2023-08-23 Removed alternate prop pitch for development in another branch
    [prop_pitch_nrf24.kicad_pcb, prop_pitch_nrf24.kicad_sch]
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2023-08-23 Initial upload of redesigned prop controller
    [prop_pitch_nrf24.kicad_pcb, prop_pitch_nrf24.kicad_sch]
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2023-08-25 Add new connections
    Added UART and SPI Pin connections
    [motherboard.kicad_sch]
2023-08-25 Reverted to default sheet template
    [prop_pitch_nrf24.kicad_sch]
2023-09-12 Bro where is my last update
    Added a name and some author stuff
    [power_monitor.kicad_pcb]
2023-09-12 More pretty edits
    Now that I know what the layers really are it makes a lot more sense
    [power_monitor.kicad_pcb]
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2023-09-16 Small edits
    Moved around the text on back and moved the trace by the mounting hole.
    [power_monitor.kicad_pcb]
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2023-11-01 Adding Components to motherboard
    Added HC-05 and MH-Z19 To the motherboard schematic
    [motherboard.kicad_sch]
2023-11-09 Completed First Draft of Motherboard Schematic
    Added in second bluetooth module, corrected pin allocations, fixed schematic symbols
    [motherboard.kicad_sch]
2023-11-10 Edited Headers added power and ground pins to external board headers, added ground to MC, added capictor to I2C
    [motherboard.kicad_sch]
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2023-11-10 Fixed up some schmatic symbols
    Fixed schematic symbols for hc-05 and the 6 axis IMU
    [motherboard.kicad_sch]
2023-11-10 Final motherboard schematic draft
    Made several small changes to the schematic:
    - Merged all custom symbols into one library
    - Touched up custom symbols for aesthetics and organization
    - Adjusted schematic for revised schematics
    - Added OneWire hardware to schematic
    - Removed redudant 3.3V regulator (3.3V will be supplied by control board)
    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
    [motherboard.kicad_sch]
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2023-11-20 Completed Footprint Draft
    Added pin headers for all the remaining components on the board.
    [motherboard.kicad_sch]
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2023-11-25 Edited footprints
    Edited custom footprints and completed first layout draft
    [motherboard.kicad_pcb, motherboard.kicad_sch]
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2023-11-28 Added Traces
    Added more traces to the layout
    [motherboard.kicad_pcb]
2023-11-29 Completed draft 1 of layout
    Finished laying down traces and running drc on the layout
    [motherboard.kicad_pcb]
2023-11-29 Touch ups for control board
    - Made adjustments to the placement of the decoupling capacitors for the STM32.
    - Rotated some capacitors for VBATT pour
    - Removed reference designators for most components
    - Added some labels for the main power headers
    [control.kicad_pcb]
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2023-11-29 Polished 1st Draft Layout
    Aligned vias, grouped traces, added text and graphics
    [motherboard.kicad_pcb]
2023-11-30 added name, title, company, revision # & authors
    [control.kicad_pcb, control.kicad_sch]
2023-11-30 Completed feedback for draft 1 round 1
    addded thicker traces, disconnected 3.3V from RPi, changed capacitor location, added mounting holes for RPi, added mounting holes to the board, added programming labels
    [motherboard.kicad_pcb, motherboard.kicad_sch]
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2023-12-01 Minor tweaks to motherboard
    - Changed DRC settings to allow tighter copper spacing.
    - Removed RPi 3.3V connection
    [mb_RPI.kicad_sch, motherboard.kicad_pcb, motherboard.kicad_sch]
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2023-12-02 deleted mounting hole and added rpi moutning hole
    [motherboard.kicad_sch]
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2024-02-03 Revised Motherboard design with correct programming pin connections
    Changed schematic with correct pins for programming and updated board to reflect this. Moved some traces to fit the new traces in.
    [motherboard.kicad_pcb, motherboard.kicad_sch]
2024-02-09 Status leds
    Added 3 status LEDs and resistors on the left side of the board. Moved some traces and vias but left all components locked in position.
    [motherboard.kicad_pcb, motherboard.kicad_sch]
2024-02-11 Fixed USB connections
    [motherboard.kicad_pcb, motherboard.kicad_sch]
2024-02-14 Updated Schematic
    Checked all connections on schematic compared to stm32f412 datasheet. Added labels for LEDs.
    [motherboard.kicad_sch]
2024-02-14 PCB Rev2 Layout
    PCB layout revised with ground and power pours, differential routing for USB, fixes for USB and programming pins. Passes DRC.
    [motherboard.kicad_pcb, motherboard.kicad_sch]
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2024-02-16 Touchups to revised control board
    - Removed redundant battery connection in schematic
    - Added labels to programming signals in schematic
    - Added "Rev. ##" label on board
    [control.kicad_pcb, control.kicad_sch]
2024-02-16 Touched up layout
    Updated title block and made revision label used title block value
    [motherboard.kicad_pcb]
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2024-03-22 Added extra LEDs, replaced Voltage reg., added redundant SW, reviewed USB placement
    Added many new features
    [flight_stick.kicad_sch, motherboard.kicad_pcb]
2024-03-23 updated 3rd revision
    reduced the number of strain gauges and updated the schematic and placed the initial layout without traces.
    [flight_stick.kicad_pcb, flight_stick.kicad_sch]
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2024-03-25 Touched up block diagram
    Minor changes:
    - Fixed spelling of "Strain Gauge" in a few locations
    - Changed HX711 protocol labels from "SPI" to "Digital" for accuracy
    - Fixed width of PWM arrow to the Power Assit block
    - Added number of HX711s to the flightstick block
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2024-04-14 Motherboard Revision 3 Initial Commit
    Motherboard updated with pull up resistors, decoupling capacitors, on board regulator, op-amp for magnetic encoder, and more.
    [motherboard.kicad_pcb, motherboard.kicad_sch]
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2024-04-17 Made Recommended changes
    From savo:
    C11 is a decoupling capacitor for one of the HX711s, it should be closer to it
    You can get rid of two of the mounting holes. Two are enough.
    Try to bring the USB stuff closer to the STM32, since it operates at high speed and we should keep the connections short.
    Similarly try to bring the programming header closer to the STM32.
    You can move the button stuff further from the STM32, those will be operated at kHz which is "slow"
    The resistors you picked for the LEDs are a fair bit smaller than needed, 100+ Ohms is good.
    No need for the pulldown R34
    Power LEDs are cool, but maybe just one on the 3V3 rail is enough since thats the critical line. You can probabl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
    [flight_stick.kicad_pcb, flight_stick.kicad_sch]
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2024-05-14 Touched up rev3 flight stick
    Needed to complete the 5V routing to the USB/I2C header. Also repositioned the reset button.
    [flight_stick.kicad_pcb]
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2024-05-24 Changed voltage regulator footprint
    Removed thermal vias since they were too small for manufacturing.
    [motherboard.kicad_pcb, motherboard.kicad_sch]
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2024-06-29 Fixed power LED labelling
    Power indication LEDs had their part references changed to labels causing DRC issues and inconsistency in the board.
    Fixed the references to be LED# again and added label text for the power lines.
    [control.kicad_pcb]
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
